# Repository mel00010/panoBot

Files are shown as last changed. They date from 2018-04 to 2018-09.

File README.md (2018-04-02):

# panoBot

## Summary of main responsiblities
- John (OLED display)
- Ben (PID loop)
- Zach (Servo movement/control)
- Justin (Button control)
- Mel (Hardware, main control flow)

## Update Monday March 12th
- Entire directory structure refactored to add some consistency
- Wrote Camera library to control the camera
- Started work on writing main()
- Wrote numerous utility functions as the avr-g++ compiler does not provide any of the C++ standard library headers
- Expanded and updated build system
- Modified build process to enable debugging, and create a target with debugging symbols included.  

## Update Sunday March 11th
- Servo controls for the most part figured out, still need to fine tune timings with hardwarde, but servos now have the ability to update/calculate their angles

- Buttons are finished may need to fine tune the debounce timings as needed, but outputting the correct information

- Screen code started, menu logic is still needed.

- Hardware debugger has arrived and finishing up final hardware configuration, planning on fine tuning with the hardware the upcomming week

- certain moving parts/cases are needing to be printed, planning on doing this Monday 03/12

## Update Sunday March 4th
- Update on project status: Due to hardware issues, the project has been reformed... we are now focusing on the firmware (Interfacing the Arduino board with the physical components: Buttons, toggle switch, servo, led display)

- The board as of Friday March 2 has been updated and is ready to undergo final testing. We now have a proper debugger for the board and can begin testing soft/hardware to ensure it will work properly.

- A PID(Proportion integral derivative) loop has been created to ensure servos will move to the appropriate place

- Button/Toggle switches are 90% done, all code is working (abstractly) but delay timings and port/switch numbers will be fine tuned later.

- Button debounce(noise reduction) implemented through software, this may need to be fine tuned, but will update as needed

- Servo timings have been selected, the prescaler , WGM (Wave Generation Mode) type has been selected 

- Physical display has minimal work, but as the deadline moves closer and members finish we will have multiple people working on the display

- Current goals: Finish rough draft of firmware, test with the board and fine tune timings. 

- Update although Google protobuf was originally planned as part of the project, as a way to interact with the panobot through a laptop, this has been put on hold while we ensure the firmware works properly. If adequate time is left over we will resume working on laptop/panobot interactions

## Update Sunday February 26th

- Spent most of the week working on hardware, the majority of which is complete
- Protobuff created for servo movement , camera communication
- GUI Template done, without buttons, this will be on hold until command line is more refined
(Zach , Ben , Justin, Mel)

## Update Sunday February 18th

- decided on google protobuf syntax/types
- Starting/Stopping 
- Movement:
	Elevation angle, servo angle
- Camera interactions:
	Focus
	Shutter
We all went through the tutorial for protobuf and made sure it is installed correctly/we are all using the correct documentation.

## The circuit board has been designed and built.

## Decided on using GTK+ for GUI, began work on GUI, currently in a rough mockup stage.
(Zach, Ben, Justin , Mel, John)

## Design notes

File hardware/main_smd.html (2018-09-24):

Partlist exported from /home/mel/eagle/projects/panoBot/main_smd.sch at 6/14/18 3:39 AM

Part | Value | Device | Package | Description | ALLIED_NUMBER | ALLIED_PRICE/STOCK | ARROW_PART_NUMBER | ARROW_PRICE/STOCK | AVAILABILITY | CENTERLINE_PITCH | COMMENT | DATASHEET | DESCRIPTION | DISTRIBUTOR1 | DISTRIBUTOR2 | GEOMETRY_HEIGHT | HEIGHT | MANUFACTURER | MANUFACTURER_NAME | MANUFACTURER_PART_NUMBER | MF | MP | MPN | NUMBER_OF_POSITIONS | ORDERCODE-DISTRI1 | ORDERCODE-DISTRI2 | ORDERCODE-MANU1 | PACKAGE | PARTNUMBER | PRICE | PRODUCT_TYPE | PROD_ID | RS_PART_NUMBER | RS_PRICE/STOCK | SF_ID | SPICEPREFIX | VALUE | VENDOR
+ | | 3,81/1,1 | 3,81/1,1 | THROUGH-HOLE PAD
- | | 3,81/1,1 | 3,81/1,1 | THROUGH-HOLE PAD
C1 | 0.1uF | 0.1UF-0603-100V-10% | 0603 | 0.1µF ceramic capacitors | | | | | | | | | | | | | | | | | | | | | | | | | | | | CAP-08390 | | | | | 0.1uF
C2 | 1.0uF | 1.0UF-0603-16V-10% | 0603 | 1µF ceramic capacitors | | | | | | | | | | | | | | | | | | | | | | | | | | | | CAP-00868 | | | | | 1.0uF
C3 | 10nF | 10NF-0603-50V-10% | 0603 | 0.01uF/10nF/10,000pF ceramic capacitors | | | | | | | | | | | | | | | | | | | | | | | | | | | | CAP-00867 | | | | | 10nF
C4 | 0.1uF | 0.1UF-0402-16V-10% | 0402 | 0.1µF ceramic capacitors | | | | | | | | | | | | | | | | | | | | | | | | | | | | CAP-12416 | | | | | 0.1uF
C5 | 0.1uF | 0.1UF-0402-16V-10% | 0402 | 0.1µF ceramic capacitors | | | | | | | | | | | | | | | | | | | | | | | | | | | | CAP-12416 | | | | | 0.1uF
C6 | 10uF | 10UF-0603-6.3V-20% | 0603 | 10.0µF ceramic capacitors | | | | | | | | | | | | | | | | | | | | | | | | | | | | CAP-11015 | | | | | 10uF
C7 | 0.1uF | 0.1UF-0402-16V-10% | 0402 | 0.1µF ceramic capacitors | | | | | | | | | | | | | | | | | | | | | | | | | | | | CAP-12416 | | | | | 0.1uF
C8 | 470nF | 470NF-0402-16V-10% | 0402 | 0.47uF/470nF ceramic capacitors | | | | | | | | | | | | | | | | | | | | | | | | | | | | CAP-09041 | | | | | 470nF
C9 | 0.1uF | 0.1UF-0402-16V-10% | 0402 | 0.1µF ceramic capacitors | | | | | | | | | | | | | | | | | | | | | | | | | | | | CAP-12416 | | | | | 0.1uF
C10 | 10nF | 10NF-0603-50V-10% | 0603 | 0.01uF/10nF/10,000pF ceramic capacitors | | | | | | | | | | | | | | | | | | | | | | | | | | | | CAP-00867 | | | | | 10nF
C11 | 10nF | 10NF-0603-50V-10% | 0603 | 0.01uF/10nF/10,000pF ceramic capacitors | | | | | | | | | | | | | | | | | | | | | | | | | | | | CAP-00867 | | | | | 10nF
C12 | 10nF | 10NF-0603-50V-10% | 0603 | 0.01uF/10nF/10,000pF ceramic capacitors | | | | | | | | | | | | | | | | | | | | | | | | | | | | CAP-00867 | | | | | 10nF
C13 | 10uF | 10UF-1210-50V-20% | 1210 | 10.0µF ceramic capacitors | | | | | | | | | | | | | | | | | | | | | | | | | | | | CAP-09824 | | | | | 10uF
C14 | 0.22uF | 0.22UF-0603-25V-10% | 0603 | 0.22µF ceramic capacitors | | | | | | | | | | | | | | | | | | | | | | | | | | | | CAP-07822 | | | | | 0.22uF
C15 | 0.1uF | 0.1UF-0402-16V-10% | 0402 | 0.1µF ceramic capacitors | | | | | | | | | | | | | | | | | | | | | | | | | | | | CAP-12416 | | | | | 0.1uF
C16 | 0.22uF | 0.22UF-0603-25V-10% | 0603 | 0.22µF ceramic capacitors | | | | | | | | | | | | | | | | | | | | | | | | | | | | CAP-07822 | | | | | 0.22uF
C17 | 0.1uF | 0.1UF-0402-16V-10% | 0402 | 0.1µF ceramic capacitors | | | | | | | | | | | | | | | | | | | | | | | | | | | | CAP-12416 | | | | | 0.1uF
C18 | 0.22uF | 0.22UF-0603-25V-10% | 0603 | 0.22µF ceramic capacitors | | | | | | | | | | | | | | | | | | | | | | | | | | | | CAP-07822 | | | | | 0.22uF
C19 | 1.0uF | 1.0UF-1206-50V-10% | 1206 | 1µF ceramic capacitors | | | | | | | | | | | | | | | | | | | | | | | | | | | | CAP-09822 | | | | | 1.0uF
C20 | 10nF | 10NF-0603-50V-10% | 0603 | 0.01uF/10nF/10,000pF ceramic capacitors | | | | | | | | | | | | | | | | | | | | | | | | | | | | CAP-00867 | | | | | 10nF
C21 | 0.1uF | C-EU075-052X106 | C075-052X106 | CAPACITOR, European symbol | | | | | | | | | | | | | | | | | | | | | | | | | | | | | | | | C
C22 | 1uF | CPOL-US085CS-1AR | 085CS_1AR | POLARIZED CAPACITOR, American symbol
C23 | 10uF | CPOL-US085CS-1AR | 085CS_1AR | POLARIZED CAPACITOR, American symbol
C24 | 10nF | 10NF-0603-50V-10% | 0603 | 0.01uF/10nF/10,000pF ceramic capacitors | | | | | | | | | | | | | | | | | | | | | | | | | | | | CAP-00867 | | | | | 10nF
C25 | 10nF | 10NF-0603-50V-10% | 0603 | 0.01uF/10nF/10,000pF ceramic capacitors | | | | | | | | | | | | | | | | | | | | | | | | | | | | CAP-00867 | | | | | 10nF
C26 | 0.1uF | 0.1UF-0402-16V-10% | 0402 | 0.1µF ceramic capacitors | | | | | | | | | | | | | | | | | | | | | | | | | | | | CAP-12416 | | | | | 0.1uF
C27 | 0.1uF | 0.1UF-0402-16V-10% | 0402 | 0.1µF ceramic capacitors | | | | | | | | | | | | | | | | | | | | | | | | | | | | CAP-12416 | | | | | 0.1uF
C28 | 0.1uF | 0.1UF-0402-16V-10% | 0402 | 0.1µF ceramic capacitors | | | | | | | | | | | | | | | | | | | | | | | | | | | | CAP-12416 | | | | | 0.1uF
C29 | 0.1uF | 0.1UF-0402-16V-10% | 0402 | 0.1µF ceramic capacitors | | | | | | | | | | | | | | | | | | | | | | | | | | | | CAP-12416 | | | | | 0.1uF
C30 | 4.7uF | 4.7UF0603 | 0603 | 4.7µF ceramic capacitors | | | | | | | | | | | | | | | | | | | | | | | | | | | | CAP-08280 | | | | | 4.7uF
C31 | 10nF | 10NF-0603-50V-10% | 0603 | 0.01uF/10nF/10,000pF ceramic capacitors | | | | | | | | | | | | | | | | | | | | | | | | | | | | CAP-00867 | | | | | 10nF
C32 | 10nF | 10NF-0603-50V-10% | 0603 | 0.01uF/10nF/10,000pF ceramic capacitors | | | | | | | | | | | | | | | | | | | | | | | | | | | | CAP-00867 | | | | | 10nF
C33 | 0.1uF | 0.1UF-0603-25V-(+80/-20%) | 0603 | 0.1µF ceramic capacitors | | | | | | | | | | | | | | | | | | | | | | | | | | | | CAP-00810 | | | | | 0.1uF
C34 | 0.1uF | 0.1UF-0603-25V-(+80/-20%) | 0603 | 0.1µF ceramic capacitors | | | | | | | | | | | | | | | | | | | | | | | | | | | | CAP-00810 | | | | | 0.1uF
C35 | 10nF | 10NF-0603-50V-10% | 0603 | 0.01uF/10nF/10,000pF ceramic capacitors | | | | | | | | | | | | | | | | | | | | | | | | | | | | CAP-00867 | | | | | 10nF
C36 | 10nF | 10NF-0603-50V-10% | 0603 | 0.01uF/10nF/10,000pF ceramic capacitors | | | | | | | | | | | | | | | | | | | | | | | | | | | | CAP-00867 | | | | | 10nF
C37 | 10nF | 10NF-0603-50V-10% | 0603 | 0.01uF/10nF/10,000pF ceramic capacitors | | | | | | | | | | | | | | | | | | | | | | | | | | | | CAP-00867 | | | | | 10nF
C38 | 10uF | 10UF-1210-50V-20% | 1210 | 10.0µF ceramic capacitors | | | | | | | | | | | | | | | | | | | | | | | | | | | | CAP-09824 | | | | | 10uF
C39 | 0.1uF | 0.1UF-0603-100V-10% | 0603 | 0.1µF ceramic capacitors | | | | | | | | | | | | | | | | | | | | | | | | | | | | CAP-08390 | | | | | 0.1uF
C40 | 10uF | 10UF-1210-50V-20% | 1210 | 10.0µF ceramic capacitors | | | | | | | | | | | | | | | | | | | | | | | | | | | | CAP-09824 | | | | | 10uF
C41 | 0.1uF | 0.1UF-0603-100V-10% | 0603 | 0.1µF ceramic capacitors | | | | | | | | | | | | | | | | | | | | | | | | | | | | CAP-08390 | | | | | 0.1uF
C42 | 10uF | 10UF-1210-50V-20% | 1210 | 10.0µF ceramic capacitors | | | | | | | | | | | | | | | | | | | | | | | | | | | | CAP-09824 | | | | | 10uF
C43 | 0.1uF | 0.1UF-0603-100V-10% | 0603 | 0.1µF ceramic capacitors | | | | | | | | | | | | | | | | | | | | | | | | | | | | CAP-08390 | | | | | 0.1uF
C44 | 22UF-1210-16V-20% | 22UF-1210-16V-20% | 1210 | 22µF ceramic capacitors
C45 | 22UF-1210-16V-20% | 22UF-1210-16V-20% | 1210 | 22µF ceramic capacitors
C46 | 22UF-1210-16V-20% | 22UF-1210-16V-20% | 1210 | 22µF ceramic capacitors
C47 | 22UF-1210-16V-20% | 22UF-1210-16V-20% | 1210 | 22µF ceramic capacitors
C48 | 22UF-1210-16V-20% | 22UF-1210-16V-20% | 1210 | 22µF ceramic capacitors
C49 | 22UF-1210-16V-20% | 22UF-1210-16V-20% | 1210 | 22µF ceramic capacitors
C50 | 0.1uF | 0.1UF-0402-16V-10% | 0402 | 0.1µF ceramic capacitors | | | | | | | | | | | | | | | | | | | | | | | | | | | | CAP-12416 | | | | | 0.1uF
C51 | 0.1uF | 0.1UF-0402-16V-10% | 0402 | 0.1µF ceramic capacitors | | | | | | | | | | | | | | | | | | | | | | | | | | | | CAP-12416 | | | | | 0.1uF
C52 | 0.1uF | 0.1UF-0402-16V-10% | 0402 | 0.1µF ceramic capacitors | | | | | | | | | | | | | | | | | | | | | | | | | | | | CAP-12416 | | | | | 0.1uF
C53 | 1800pF | C-EUC0402 | C0402 | CAPACITOR, European symbol
C54 | 91pF | C-EUC0402 | C0402 | CAPACITOR, European symbol
C55 | 2200pF | C-EUC0402 | C0402 | CAPACITOR, European symbol
C56 | 100pF | C-EUC0402 | C0402 | CAPACITOR, European symbol
C57 | 5600pF | C-EUC0402 | C0402 | CAPACITOR, European symbol
C58 | 330pF | C-EUC0402 | C0402 | CAPACITOR, European symbol
C59 | 0.1uF | 0.1UF-0603-25V-5% | 0603 | 0.1µF ceramic capacitors | | | | | | | | | | | | | | | | | | | | | | | | | | | | CAP-08604 | | | | | 0.1uF
C60 | 0.1uF | 0.1UF-0603-25V-5% | 0603 | 0.1µF ceramic capacitors | | | | | | | | | | | | | | | | | | | | | | | | | | | | CAP-08604 | | | | | 0.1uF
C61 | 0.1uF | 0.1UF-0603-25V-5% | 0603 | 0.1µF ceramic capacitors | | | | | | | | | | | | | | | | | | | | | | | | | | | | CAP-08604 | | | | | 0.1uF
C62 | 220pF | C-EUC0402 | C0402 | CAPACITOR, European symbol
C63 | 220pF | C-EUC0402 | C0402 | CAPACITOR, European symbol
C64 | 1.0uF | 1.0UF-1206-50V-10% | 1206 | 1µF ceramic capacitors | | | | | | | | | | | | | | | | | | | | | | | | | | | | CAP-09822 | | | | | 1.0uF
C65 | 10uF | 10UF-1210-50V-20% | 1210 | 10.0µF ceramic capacitors | | | | | | | | | | | | | | | | | | | | | | | | | | | | CAP-09824 | | | | | 10uF
C66 | 1.0uF | 1.0UF-1206-50V-10% | 1206 | 1µF ceramic capacitors | | | | | | | | | | | | | | | | | | | | | | | | | | | | CAP-09822 | | | | | 1.0uF
C67 | 1.0uF | 1.0UF-1206-50V-10% | 1206 | 1µF ceramic capacitors | | | | | | | | | | | | | | | | | | | | | | | | | | | | CAP-09822 | | | | | 1.0uF
C68 | 1.0uF | 1.0UF-1206-50V-10% | 1206 | 1µF ceramic capacitors | | | | | | | | | | | | | | | | | | | | | | | | | | | | CAP-09822 | | | | | 1.0uF
C69 | 22UF-1210-16V-20% | 22UF-1210-16V-20% | 1210 | 22µF ceramic capacitors
C70 | 10uF | 10UF-1210-50V-20% | 1210 | 10.0µF ceramic capacitors | | | | | | | | | | | | | | | | | | | | | | | | | | | | CAP-09824 | | | | | 10uF
C71 | 0.1uF | 0.1UF-0603-25V-5% | 0603 | 0.1µF ceramic capacitors | | | | | | | | | | | | | | | | | | | | | | | | | | | | CAP-08604 | | | | | 0.1uF
C72 | 0.1uF | 0.1UF-0603-25V-5% | 0603 | 0.1µF ceramic capacitors | | | | | | | | | | | | | | | | | | | | | | | | | | | | CAP-08604 | | | | | 0.1uF
C73 | 0.22uF | 0.22UF-0603-25V-10% | 0603 | 0.22µF ceramic capacitors | | | | | | | | | | | | | | | | | | | | | | | | | | | | CAP-07822 | | | | | 0.22uF
C74 | 1.0uF | 1.0UF-0402-16V-10% | 0402 | 1µF ceramic capacitors | | | | | | | | | | | | | | | | | | | | | | | | | | | | CAP-12417 | | | | | 1.0uF
C75 | 10nF | 10NF-0603-50V-10% | 0603 | 0.01uF/10nF/10,000pF ceramic capacitors | | | | | | | | | | | | | | | | | | | | | | | | | | | | CAP-00867 | | | | | 10nF
D1 | MBRS340T3 | MBRS340T3 | SMC | SCHOTTKY BARRIER RECTIFIER 3.0 AMPERES 20, 30, 40 VOLT
D2 | 1N4002 | 1N4004 | DO41-10 | DIODE
D3 | 1N4002 | 1N4004 | DO41-10 | DIODE
FB1 | 30Ω/1.8A | FERRITE_BEAD-0603 | 0603 | Ferrite Bead (blocks, cores, rings, chokes, etc.) | | | | | | | | | | | | | | | | | | | | | | | | | | | | NDUC-07859 | | | | | 30Ω/1.8A
FOCUS | 4N35S | 4N35S | SOT23-6
IC0 | STM32F313VCT6 | STM32F313VCT6 | QFP50P1600X1600X160-100N
IC1 | S1315F8_RAW | S1315F8_RAW | S1315F8_SMT
IC2 | TMC262-LA | TMC262-LA | TMC_QFN32_0.5_5.0X5.0 | Energy saving high resolution microstepping two phase stepper driver with Step/Dir, SPI, up to 60V, QFN32(5x5) | | | | | | | | http://www_trinamic_com/_scripts/download_php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 | Energy saving high resolution microstepping two phase stepper driver with Step/Dir, SPI, up to 60V, QFN32(5x5) | Digikey | Farnell | 0,9mm | | TRINAMIC | | | | | | | 1460-1044-ND | 1858307 | TMC262-LA | | | | | | | | | | TMC262-LA
IC3 | TMC262-LA | TMC262-LA | TMC_QFN32_0.5_5.0X5.0 | Energy saving high resolution microstepping two phase stepper driver with Step/Dir, SPI, up to 60V, QFN32(5x5) | | | | | | | | http://www_trinamic_com/_scripts/download_php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 | Energy saving high resolution microstepping two phase stepper driver with Step/Dir, SPI, up to 60V, QFN32(5x5) | Digikey | Farnell | 0,9mm | | TRINAMIC | | | | | | | 1460-1044-ND | 1858307 | TMC262-LA | | | | | | | | | | TMC262-LA
IC4 | TMC262-LA | TMC262-LA | TMC_QFN32_0.5_5.0X5.0 | Energy saving high resolution microstepping two phase stepper driver with Step/Dir, SPI, up to 60V, QFN32(5x5) | | | | | | | | http://www_trinamic_com/_scripts/download_php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 | Energy saving high resolution microstepping two phase stepper driver with Step/Dir, SPI, up to 60V, QFN32(5x5) | Digikey | Farnell | 0,9mm | | TRINAMIC | | | | | | | 1460-1044-ND | 1858307 | TMC262-LA | | | | | | | | | | TMC262-LA
IC5 | TMC424 | TMC424 | TMC_TQFP100_0.5_14X14 | Serial triple Incremental Encoder Interface; TQ100 | | | | | | | | http://www_trinamic_com/_scripts/download_php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 | Serial triple Incremental Encoder Interface | TQ100 | Digikey | Farnell | 1_6mm | | TRINAMIC | | | | | | | 1460-1046-ND | | TMC424 | | | | | | | | | | TMC424
IC6 | TMC429-PI24 | TMC429-PI24 | TMC_SO24_SOT137-1_1.27_15.5X7.5 | Intelligent Triple Stepper Motor Controller with SPI, Step/Dir, SOP24 | | | | | | | | http://www_trinamic_com/_scripts/download_php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 | Intelligent Triple Stepper Motor Controller with SPI, Step/Dir, SOP24 | Digikey | Farnell | 2,65mm | | TRINAMIC | | | | | | | 1460-1058-5-ND | 1858309 | TMC429-PI24 | | | | | | | | | | TMC429-PI24
IC8 | LM317MBSTT3 | LM317MBSTT3 | SOT223 | 500 mA Adjustable Output Positive Voltage Regulator | | | | | | | | | | | | | | | | | | | | | | | | | LM317M
J1 | POWER_JACKPTH_BREAD | POWER_JACKPTH_BREAD | POWER_JACK_PTH_BREAD | Power Jack Connector | | | | | | | | | | | | | | | | | | | | | | | | | | | | PRT-10811
J2 | | CONN_05X2SHD_LOCK | 2X5-SHROUDED_LOCK | Multi connection point. Often used as Generic Header-pin footprint for 0.1 inch spaced/style header connections | | | | | | | | | | | | | | | | | | | | | | | | | | | | CONN-08671 | | | PRT-08506
J3 | Motor Coil B | SCREW-TERMINAL-GREEN(2P-5.0) | H2-5.0-10.5X8.0MM | 320110031 | | | | | | | | | | | | | | | | | | | | | | | | | | | | | | | | | GREEN-2P-5.0
J4 | Motor Coil A | SCREW-TERMINAL-GREEN(2P-5.0) | H2-5.0-10.5X8.0MM | 320110031 | | | | | | | | | | | | | | | | | | | | | | | | | | | | | | | | | GREEN-2P-5.0
J5 | 73100-0114 | 73100-0114 | 73100-0114 | Molex Right Angle 50ohm | 70357943 | http://www.alliedelec.com/molex-incorporated-73100-0114/70357943/ | 73100-0114 | http://uk.rs-online.com/web/p/products/7595252P | | | | | Molex Right Angle 50ohm | | | | mm | | Molex | 73100-0114 | | | | | | | | | | | | | 7595252P | http://uk.rs-online.com/web/p/products/7595252P
J8 | | CONN_05 | 1X05 | Multi connection point. Often used as Generic Header-pin footprint for 0.1 inch spaced/style header connections
J9 | Motor Coil B | SCREW-TERMINAL-GREEN(2P-5.0) | H2-5.0-10.5X8.0MM | 320110031 | | | | | | | | | | | | | | | | | | | | | | | | | | | | | | | | | GREEN-2P-5.0
J10 | Motor Coil A | SCREW-TERMINAL-GREEN(2P-5.0) | H2-5.0-10.5X8.0MM | 320110031 | | | | | | | | | | | | | | | | | | | | | | | | | | | | | | | | | GREEN-2P-5.0
J11 | Motor Coil B | SCREW-TERMINAL-GREEN(2P-5.0) | H2-5.0-10.5X8.0MM | 320110031 | | | | | | | | | | | | | | | | | | | | | | | | | | | | | | | | | GREEN-2P-5.0
J12 | Motor Coil A | SCREW-TERMINAL-GREEN(2P-5.0) | H2-5.0-10.5X8.0MM | 320110031 | | | | | | | | | | | | | | | | | | | | | | | | | | | | | | | | | GREEN-2P-5.0
J13 | | CONN_05 | 1X05 | Multi connection point. Often used as Generic Header-pin footprint for 0.1 inch spaced/style header connections
J14 | | CONN_05 | 1X05 | Multi connection point. Often used as Generic Header-pin footprint for 0.1 inch spaced/style header connections
JP1 | | JP1Q | JP1 | JUMPER
L3 | 10UH-225MA | SMD-INDUCTOR-10UH-225MA-10%(0806) | L0806 | 303010042 | | | | | | | | | | | | | | | | | | | LQH2MCN100K02L | | | | | | | | | | | | | | 10UH-225MA
L4 | 10UH-225MA | SMD-INDUCTOR-10UH-225MA-10%(0806) | L0806 | 303010042 | | | | | | | | | | | | | | | | | | | LQH2MCN100K02L | | | | | | | | | | | | | | 10UH-225MA
L5 | 10UH-225MA | SMD-INDUCTOR-10UH-225MA-10%(0806) | L0806 | 303010042 | | | | | | | | | | | | | | | | | | | LQH2MCN100K02L | | | | | | | | | | | | | | 10UH-225MA
P1 | 1-2295018-2 | 1-2295018-2 | TE_1-2295018-2 | Conn USB Type C RCP 12 POS Solder RA SMD 12 Terminal 1 Port T/R | | | | | Good | .5 mm[.019 in] | 1-2295018-2 | | USB TYPE C, REC OFFSET 0.65MM DUAL SMT | | | | | | | | TE Connectivity | 1-2295018-2 | | 24 | | | | None | | 1.70 USD | Connector
Q1 | AOD4189 | AOD4189 | TO252
Q2 | AOD4189 | AOD4189 | TO252
Q3 | AOD4184A | AOD4184A | TO252
Q4 | AOD4184A | AOD4184A | TO252
Q5 | AOD4184A | AOD4184A | TO252
Q6 | AOD4184A | AOD4184A | TO252
Q7 | AOD4189 | AOD4189 | TO252
Q8 | AOD4189 | AOD4189 | TO252
Q9 | AOD4189 | AOD4189 | TO252
Q10 | AOD4189 | AOD4189 | TO252
Q11 | AOD4184A | AOD4184A | TO252
Q12 | AOD4184A | AOD4184A | TO252
Q13 | AOD4184A | AOD4184A | TO252
Q14 | AOD4184A | AOD4184A | TO252
Q15 | AOD4189 | AOD4189 | TO252
Q16 | AOD4189 | AOD4189 | TO252
Q17 | AOD4189 | AOD4189 | TO252
Q18 | AOD4189 | AOD4189 | TO252
Q19 | AOD4184A | AOD4184A | TO252
Q20 | AOD4184A | AOD4184A | TO252
Q21 | AOD4184A | AOD4184A | TO252
Q22 | AOD4184A | AOD4184A | TO252
Q23 | AOD4189 | AOD4189 | TO252
Q24 | AOD4189 | AOD4189 | TO252
R1 | 100K | 100KOHM-0402-1/16W-1% | 0402 | 100kΩ resistor | | | | | | | | | | | | | | | | | | | | | | | | | | | | RES-13495 | | | | | 100K
R6 | 10k | 10KOHM-0603-1/10W-1% | 0603 | 10kΩ resistor | | | | | | | | | | | | | | | | | | | | | | | | | | | | RES-00824 | | | | | 10k
R7 | 0.1 | 0.1OHM-1210-1/2W-1% | 1210 | 0.1Ω resistor | | | | | | | | | | | | | | | | | | | | | | | | | | | | RES-12374 | | | | | 0.1
R8 | 0.1 | 0.1OHM-1210-1/2W-1% | 1210 | 0.1Ω resistor | | | | | | | | | | | | | | | | | | | | | | | | | | | | RES-12374 | | | | | 0.1
R9 | 220 | 220OHM-0603-1/10W-1% | 0603 | 220Ω resistor | | | | | | | | | | | | | | | | | | | | | | | | | | | | RES-07861 | | | | | 220
R10 | 220 | 220OHM-0603-1/10W-1% | 0603 | 220Ω resistor | | | | | | | | | | | | | | | | | | | | | | | | | | | | RES-07861 | | | | | 220
R11 | 10k | 10KOHM-0603-1/10W-1% | 0603 | 10kΩ resistor | | | | | | | | | | | | | | | | | | | | | | | | | | | | RES-00824 | | | | | 10k
R12 | 10k | 10KOHM-0603-1/10W-1% | 0603 | 10kΩ resistor | | | | | | | | | | | | | | | | | | | | | | | | | | | | RES-00824 | | | | | 10k
R13 | 10k | 10KOHM-0603-1/10W-1% | 0603 | 10kΩ resistor | | | | | | | | | | | | | | | | | | | | | | | | | | | | RES-00824 | | | | | 10k
R14 | 10k | 10KOHM-0603-1/10W-1% | 0603 | 10kΩ resistor | | | | | | | | | | | | | | | | | | | | | | | | | | | | RES-00824 | | | | | 10k
R15 | 10 | 10OHM-1206-1/4W-1% | 1206 | 10Ω resistor | | | | | | | | | | | | | | | | | | | | | | | | | | | | RES-08705 | | | | | 10
R16 | 10 | 10OHM-1206-1/4W-1% | 1206 | 10Ω resistor | | | | | | | | | | | | | | | | | | | | | | | | | | | | RES-08705 | | | | | 10
R17 | 10k | 10KOHM-0603-1/10W-1% | 0603 | 10kΩ resistor | | | | | | | | | | | | | | | | | | | | | | | | | | | | RES-00824 | | | | | 10k
R18 | 10k | 10KOHM-0603-1/10W-1% | 0603 | 10kΩ resistor | | | | | | | | | | | | | | | | | | | | | | | | | | | | RES-00824 | | | | | 10k
R19 | 0.1 | 0.1OHM-1210-1/2W-1% | 1210 | 0.1Ω resistor | | | | | | | | | | | | | | | | | | | | | | | | | | | | RES-12374 | | | | | 0.1
R20 | 0.1 | 0.1OHM-1210-1/2W-1% | 1210 | 0.1Ω resistor | | | | | | | | | | | | | | | | | | | | | | | | | | | | RES-12374 | | | | | 0.1
R21 | 1M | 1MOHM-0603-1/4W-5% | 0603 | 1MΩ resistor | | | | | | | | | | | | | | | | | | | | | | | | | | | | RES-07868 | | | | | 1M
R22 | 10k | 10KOHM-0603-1/10W-1% | 0603 | 10kΩ resistor | | | | | | | | | | | | | | | | | | | | | | | | | | | | RES-00824 | | | | | 10k
R23 | 0.1 | 0.1OHM-1210-1/2W-1% | 1210 | 0.1Ω resistor | | | | | | | | | | | | | | | | | | | | | | | | | | | | RES-12374 | | | | | 0.1
R24 | 0.1 | 0.1OHM-1210-1/2W-1% | 1210 | 0.1Ω resistor | | | | | | | | | | | | | | | | | | | | | | | | | | | | RES-12374 | | | | | 0.1
R25 | 10 | 10OHM-1206-1/4W-1% | 1206 | 10Ω resistor | | | | | | | | | | | | | | | | | | | | | | | | | | | | RES-08705 | | | | | 10
R26 | 10 | 10OHM-1206-1/4W-1% | 1206 | 10Ω resistor | | | | | | | | | | | | | | | | | | | | | | | | | | | | RES-08705 | | | | | 10
R27 | 100k | 100KOHM-0603-1/10W-1% | 0603 | 100kΩ resistor | | | | | | | | | | | | | | | | | | | | | | | | | | | | RES-07828 | | | | | 100k
R28 | 0.01R | RESISTOR0805 | 0805 | Generic Resistor Package
R29 | 240Ω | R-US_M0805 | M0805 | RESISTOR, American symbol
R30 | 48Ω | R-US_M0805 | M0805 | RESISTOR, American symbol
R31 | 10k | 10KOHM-0603-1/10W-1% | 0603 | 10kΩ resistor | | | | | | | | | | | | | | | | | | | | | | | | | | | | RES-00824 | | | | | 10k
R32 | 10k | 10KOHM-0603-1/10W-1% | 0603 | 10kΩ resistor | | | | | | | | | | | | | | | | | | | | | | | | | | | | RES-00824 | | | | | 10k
R33 | 10 | 10OHM-1206-1/4W-1% | 1206 | 10Ω resistor | | | | | | | | | | | | | | | | | | | | | | | | | | | | RES-08705 | | | | | 10
R34 | 10 | 10OHM-1206-1/4W-1% | 1206 | 10Ω resistor | | | | | | | | | | | | | | | | | | | | | | | | | | | | RES-08705 | | | | | 10
R37 | 1M | 1MOHM-0603-1/4W-5% | 0603 | 1MΩ resistor | | | | | | | | | | | | | | | | | | | | | | | | | | | | RES-07868 | | | | | 1M
R38 | 1M | 1MOHM-0603-1/4W-5% | 0603 | 1MΩ resistor | | | | | | | | | | | | | | | | | | | | | | | | | | | | RES-07868 | | | | | 1M
R39 | 47k | 47KOHM-0603-1/10W-1% | 0603 | 47kΩ resistor | | | | | | | | | | | | | | | | | | | | | | | | | | | | RES-07871 | | | | | 47k
R40 | 47k | 47KOHM-0603-1/10W-1% | 0603 | 47kΩ resistor | | | | | | | | | | | | | | | | | | | | | | | | | | | | RES-07871 | | | | | 47k
R41 | 47k | 47KOHM-0603-1/10W-1% | 0603 | 47kΩ resistor | | | | | | | | | | | | | | | | | | | | | | | | | | | | RES-07871 | | | | | 47k
R42 | 9.53k | RESISTOR0603 | 0603 | Generic Resistor Package
R43 | 8.45k | RESISTOR0603 | 0603 | Generic Resistor Package
R44 | 2.74k | RESISTOR0603 | 0603 | Generic Resistor Package
R45 | 19.1k | RESISTOR0603 | 0603 | Generic Resistor Package
R46 | 100k | RESISTOR0603 | 0603 | Generic Resistor Package
R47 | 32.4k | RESISTOR0603 | 0603 | Generic Resistor Package
R48 | 100k | RESISTOR0603 | 0603 | Generic Resistor Package
R49 | 100k | RESISTOR0603 | 0603 | Generic Resistor Package
R50 | 7.15k | RESISTOR0603 | 0603 | Generic Resistor Package
R51 | 15k | 15KOHM-0603-1/10W-1% | 0603 | 15kΩ resistor | | | | | | | | | | | | | | | | | | | | | | | | | | | | RES-07854 | | | | | 15k
S1 | EN11-HSM1BF20 | EN11-HSM1BF20 | EN11HSM1BF20 | ENCODER 11MM ROTARY SW TOP ADJ | | | EN11-HSM1BF20 | | | | | | ENCODER 11MM ROTARY SW TOP ADJ | | | | 26mm | | TT Electronics/BI Magnetics | EN11-HSM1BF20
S2 | TL3342F160QG | TL3342F160QG | SW_TL3342F160QG | TL3342 Series SPST 1.6 N Round Button Gull Wing Surface Mount Tactile Switch | | | | | | | | | | | | | | E SWITCH
SCREEN1 | OLED | OLED | SIP-20
SHUTTER | 4N35S | 4N35S | SOT23-6
U$27 | CSD17309Q3 | CSD17309Q3 | DQG0008A | | | | | | | | | | | | | | | | | CSD17309Q3 | | | | | | | | | | | | | | | | | | Texas Instruments
U$28 | CSD17309Q3 | CSD17309Q3 | DQG0008A | | | | | | | | | | | | | | | | | CSD17309Q3 | | | | | | | | | | | | | | | | | | Texas Instruments
U$29 | TPS659821 | TPS659821 | QFN50P800X800X100-57N
U1 | TPD8S300RUKRRUK0020B_NV | TPD8S300RUKRRUK0020B_NV | RUK0020B_NV
U2 | FT232RL-REEL | FT232RL-REEL | SOP65P780X200-28N | USB Full Speed to Serial UART IC, Includes Oscillator and EEPROM - SSOP-28 | | | | | | | | | | | | | | Future Technology Devices International Ltd
U3 | CDCS502PWR | CDCS502PWR | SOP65P640X120-8N | Crystal Oscillator | | | | | Good | | | | Crystal Oscillator / Clock Generator with optional SSC 8-TSSOP -40 to 85 | | | | | | | | Texas Instruments | CDCS502PWR | | | | | | TSSOP-8 Texas Instruments | | 1.60 USD
U4 | LSM9DS1 | LSM9DS1 | PQFN24P43_350X300X102L35X23N | iNEMO inertial module: 3D accelerometer, 3D gyroscope, 3D magnetometer | | | | | Unavailable | | | | iNEMO inertial module: 3D accelerometer, 3D gyroscope, 3D magnetometer | | | | | | | | STMicroelectronics | LSM9DS1 | | | | | | None | | None
U5 | TPS54336ADRCR | TPS54336ADRCR | DRC0010J
U6 | TPS54336ADRCR | TPS54336ADRCR | DRC0010J
U7 | TPS54336ADRCR | TPS54336ADRCR | DRC0010J
X1 | STEREOJACK | STEREOJACK | STX3100 | MIC/HEADPHONE JACK
Y1 | 7B-16.000MAAJ-T | 7B-16.000MAAJ-T | 7B-16.000MAAJ-T_OSCSC500X320X105-4N | Crystal 16.0000mhz 18pf Smd | | | | | | | | | | | | | | TXC Corporation

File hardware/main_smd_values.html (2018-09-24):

Partlist exported from /home/mel/eagle/projects/panoBot/main_smd.sch at 6/14/18 3:39 AM

Qty | Value | Device | Package | Parts | Description | ALLIED_NUMBER | ALLIED_PRICE/STOCK | ARROW_PART_NUMBER | ARROW_PRICE/STOCK | AVAILABILITY | CENTERLINE_PITCH | COMMENT | DATASHEET | DESCRIPTION | DISTRIBUTOR1 | DISTRIBUTOR2 | GEOMETRY_HEIGHT | HEIGHT | MANUFACTURER | MANUFACTURER_NAME | MANUFACTURER_PART_NUMBER | MF | MP | MPN | NUMBER_OF_POSITIONS | ORDERCODE-DISTRI1 | ORDERCODE-DISTRI2 | ORDERCODE-MANU1 | PACKAGE | PARTNUMBER | PRICE | PRODUCT_TYPE | PROD_ID | RS_PART_NUMBER | RS_PRICE/STOCK | SF_ID | SPICEPREFIX | VALUE | VENDOR
2 | | 3,81/1,1 | 3,81/1,1 | +, - | THROUGH-HOLE PAD
3 | | CONN_05 | 1X05 | J8, J13, J14 | Multi connection point. Often used as Generic Header-pin footprint for 0.1 inch spaced/style header connections
1 | | CONN_05X2SHD_LOCK | 2X5-SHROUDED_LOCK | J2 | Multi connection point. Often used as Generic Header-pin footprint for 0.1 inch spaced/style header connections | | | | | | | | | | | | | | | | | | | | | | | | | | | | CONN-08671 | | | PRT-08506
1 | | JP1Q | JP1 | JP1 | JUMPER
3 | TMC262-LA | TMC262-LA | TMC_QFN32_0.5_5.0X5.0 | IC2, IC3, IC4 | Energy saving high resolution microstepping two phase stepper driver with Step/Dir, SPI, up to 60V, QFN32(5x5) | | | | | | | | http://www_trinamic_com/_scripts/download_php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 | Energy saving high resolution microstepping two phase stepper driver with Step/Dir, SPI, up to 60V, QFN32(5x5) | Digikey | Farnell | 0,9mm | | TRINAMIC | | | | | | | 1460-1044-ND | 1858307 | TMC262-LA | | | | | | | | | | TMC262-LA
1 | TMC424 | TMC424 | TMC_TQFP100_0.5_14X14 | IC5 | Serial triple Incremental Encoder Interface; TQ100 | | | | | | | | http://www_trinamic_com/_scripts/download_php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 | Serial triple Incremental Encoder Interface | TQ100 | Digikey | Farnell | 1_6mm | | TRINAMIC | | | | | | | 1460-1046-ND | | TMC424 | | | | | | | | | | TMC424
1 | TMC429-PI24 | TMC429-PI24 | TMC_SO24_SOT137-1_1.27_15.5X7.5 | IC6 | Intelligent Triple Stepper Motor Controller with SPI, Step/Dir, SOP24 | | | | | | | | http://www_trinamic_com/_scripts/download_php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 | Intelligent Triple Stepper Motor Controller with SPI, Step/Dir, SOP24 | Digikey | Farnell | 2,65mm | | TRINAMIC | | | | | | | 1460-1058-5-ND | 1858309 | TMC429-PI24 | | | | | | | | | | TMC429-PI24
1 | 0.01R | RESISTOR0805 | 0805 | R28 | Generic Resistor Package
6 | 0.1 | 0.1OHM-1210-1/2W-1% | 1210 | R7, R8, R19, R20, R23, R24 | 0.1Ω resistor | | | | | | | | | | | | | | | | | | | | | | | | | | | | RES-12374 | | | | | 0.1
13 | 0.1uF | 0.1UF-0402-16V-10% | 0402 | C4, C5, C7, C9, C15, C17, C26, C27, C28, C29, C50, C51, C52 | 0.1µF ceramic capacitors | | | | | | | | | | | | | | | | | | | | | | | | | | | | CAP-12416 | | | | | 0.1uF
4 | 0.1uF | 0.1UF-0603-100V-10% | 0603 | C1, C39, C41, C43 | 0.1µF ceramic capacitors | | | | | | | | | | | | | | | | | | | | | | | | | | | | CAP-08390 | | | | | 0.1uF
2 | 0.1uF | 0.1UF-0603-25V-(+80/-20%) | 0603 | C33, C34 | 0.1µF ceramic capacitors | | | | | | | | | | | | | | | | | | | | | | | | | | | | CAP-00810 | | | | | 0.1uF
5 | 0.1uF | 0.1UF-0603-25V-5% | 0603 | C59, C60, C61, C71, C72 | 0.1µF ceramic capacitors | | | | | | | | | | | | | | | | | | | | | | | | | | | | CAP-08604 | | | | | 0.1uF
1 | 0.1uF | C-EU075-052X106 | C075-052X106 | C21 | CAPACITOR, European symbol | | | | | | | | | | | | | | | | | | | | | | | | | | | | | | | | C
4 | 0.22uF | 0.22UF-0603-25V-10% | 0603 | C14, C16, C18, C73 | 0.22µF ceramic capacitors | | | | | | | | | | | | | | | | | | | | | | | | | | | | CAP-07822 | | | | | 0.22uF
1 | 1-2295018-2 | 1-2295018-2 | TE_1-2295018-2 | P1 | Conn USB Type C RCP 12 POS Solder RA SMD 12 Terminal 1 Port T/R | | | | | Good | .5 mm[.019 in] | 1-2295018-2 | | USB TYPE C, REC OFFSET 0.65MM DUAL SMT | | | | | | | | TE Connectivity | 1-2295018-2 | | 24 | | | | None | | 1.70 USD | Connector
1 | 1.0uF | 1.0UF-0402-16V-10% | 0402 | C74 | 1µF ceramic capacitors | | | | | | | | | | | | | | | | | | | | | | | | | | | | CAP-12417 | | | | | 1.0uF
1 | 1.0uF | 1.0UF-0603-16V-10% | 0603 | C2 | 1µF ceramic capacitors | | | | | | | | | | | | | | | | | | | | | | | | | | | | CAP-00868 | | | | | 1.0uF
5 | 1.0uF | 1.0UF-1206-50V-10% | 1206 | C19, C64, C66, C67, C68 | 1µF ceramic capacitors | | | | | | | | | | | | | | | | | | | | | | | | | | | | CAP-09822 | | | | | 1.0uF
6 | 10 | 10OHM-1206-1/4W-1% | 1206 | R15, R16, R25, R26, R33, R34 | 10Ω resistor | | | | | | | | | | | | | | | | | | | | | | | | | | | | RES-08705 | | | | | 10
1 | 100K | 100KOHM-0402-1/16W-1% | 0402 | R1 | 100kΩ resistor | | | | | | | | | | | | | | | | | | | | | | | | | | | | RES-13495 | | | | | 100K
1 | 100k | 100KOHM-0603-1/10W-1% | 0603 | R27 | 100kΩ resistor | | | | | | | | | | | | | | | | | | | | | | | | | | | | RES-07828 | | | | | 100k
3 | 100k | RESISTOR0603 | 0603 | R46, R48, R49 | Generic Resistor Package
1 | 100pF | C-EUC0402 | C0402 | C56 | CAPACITOR, European symbol
3 | 10UH-225MA | SMD-INDUCTOR-10UH-225MA-10%(0806) | L0806 | L3, L4, L5 | 303010042 | | | | | | | | | | | | | | | | | | | LQH2MCN100K02L | | | | | | | | | | | | | | 10UH-225MA
10 | 10k | 10KOHM-0603-1/10W-1% | 0603 | R6, R11, R12, R13, R14, R17, R18, R22, R31, R32 | 10kΩ resistor | | | | | | | | | | | | | | | | | | | | | | | | | | | | RES-00824 | | | | | 10k
13 | 10nF | 10NF-0603-50V-10% | 0603 | C3, C10, C11, C12, C20, C24, C25, C31, C32, C35, C36, C37, C75 | 0.01uF/10nF/10,000pF ceramic capacitors | | | | | | | | | | | | | | | | | | | | | | | | | | | | CAP-00867 | | | | | 10nF
1 | 10uF | 10UF-0603-6.3V-20% | 0603 | C6 | 10.0µF ceramic capacitors | | | | | | | | | | | | | | | | | | | | | | | | | | | | CAP-11015 | | | | | 10uF
6 | 10uF | 10UF-1210-50V-20% | 1210 | C13, C38, C40, C42, C65, C70 | 10.0µF ceramic capacitors | | | | | | | | | | | | | | | | | | | | | | | | | | | | CAP-09824 | | | | | 10uF
1 | 10uF | CPOL-US085CS-1AR | 085CS_1AR | C23 | POLARIZED CAPACITOR, American symbol
1 | 15k | 15KOHM-0603-1/10W-1% | 0603 | R51 | 15kΩ resistor | | | | | | | | | | | | | | | | | | | | | | | | | | | | RES-07854 | | | | | 15k
1 | 1800pF | C-EUC0402 | C0402 | C53 | CAPACITOR, European symbol
1 | 19.1k | RESISTOR0603 | 0603 | R45 | Generic Resistor Package
3 | 1M | 1MOHM-0603-1/4W-5% | 0603 | R21, R37, R38 | 1MΩ resistor | | | | | | | | | | | | | | | | | | | | | | | | | | | | RES-07868 | | | | | 1M
2 | 1N4002 | 1N4004 | DO41-10 | D2, D3 | DIODE
1 | 1uF | CPOL-US085CS-1AR | 085CS_1AR | C22 | POLARIZED CAPACITOR, American symbol
1 | 2.74k | RESISTOR0603 | 0603 | R44 | Generic Resistor Package
2 | 220 | 220OHM-0603-1/10W-1% | 0603 | R9, R10 | 220Ω resistor | | | | | | | | | | | | | | | | | | | | | | | | | | | | RES-07861 | | | | | 220
1 | 2200pF | C-EUC0402 | C0402 | C55 | CAPACITOR, European symbol
2 | 220pF | C-EUC0402 | C0402 | C62, C63 | CAPACITOR, European symbol
7 | 22UF-1210-16V-20% | 22UF-1210-16V-20% | 1210 | C44, C45, C46, C47, C48, C49, C69 | 22µF ceramic capacitors
1 | 240Ω | R-US_M0805 | M0805 | R29 | RESISTOR, American symbol
1 | 30Ω/1.8A | FERRITE_BEAD-0603 | 0603 | FB1 | Ferrite Bead (blocks, cores, rings, chokes, etc.) | | | | | | | | | | | | | | | | | | | | | | | | | | | | NDUC-07859 | | | | | 30Ω/1.8A
1 | 32.4k | RESISTOR0603 | 0603 | R47 | Generic Resistor Package
1 | 330pF | C-EUC0402 | C0402 | C58 | CAPACITOR, European symbol
1 | 4.7uF | 4.7UF0603 | 0603 | C30 | 4.7µF ceramic capacitors | | | | | | | | | | | | | | | | | | | | | | | | | | | | CAP-08280 | | | | | 4.7uF
1 | 470nF | 470NF-0402-16V-10% | 0402 | C8 | 0.47uF/470nF ceramic capacitors | | | | | | | | | | | | | | | | | | | | | | | | | | | | CAP-09041 | | | | | 470nF
3 | 47k | 47KOHM-0603-1/10W-1% | 0603 | R39, R40, R41 | 47kΩ resistor | | | | | | | | | | | | | | | | | | | | | | | | | | | | RES-07871 | | | | | 47k
1 | 48Ω | R-US_M0805 | M0805 | R30 | RESISTOR, American symbol
2 | 4N35S | 4N35S | SOT23-6 | FOCUS, SHUTTER
1 | 5600pF | C-EUC0402 | C0402 | C57 | CAPACITOR, European symbol
1 | 7.15k | RESISTOR0603 | 0603 | R50 | Generic Resistor Package
1 | 73100-0114 | 73100-0114 | 73100-0114 | J5 | Molex Right Angle 50ohm | 70357943 | http://www.alliedelec.com/molex-incorporated-73100-0114/70357943/ | 73100-0114 | http://uk.rs-online.com/web/p/products/7595252P | | | | | Molex Right Angle 50ohm | | | | mm | | Molex | 73100-0114 | | | | | | | | | | | | | 7595252P | http://uk.rs-online.com/web/p/products/7595252P
1 | 7B-16.000MAAJ-T | 7B-16.000MAAJ-T | 7B-16.000MAAJ-T_OSCSC500X320X105-4N | Y1 | Crystal 16.0000mhz 18pf Smd | | | | | | | | | | | | | | TXC Corporation
1 | 8.45k | RESISTOR0603 | 0603 | R43 | Generic Resistor Package
1 | 9.53k | RESISTOR0603 | 0603 | R42 | Generic Resistor Package
1 | 91pF | C-EUC0402 | C0402 | C54 | CAPACITOR, European symbol
12 | AOD4184A | AOD4184A | TO252 | Q3, Q4, Q5, Q6, Q11, Q12, Q13, Q14, Q19, Q20, Q21, Q22
12 | AOD4189 | AOD4189 | TO252 | Q1, Q2, Q7, Q8, Q9, Q10, Q15, Q16, Q17, Q18, Q23, Q24
1 | CDCS502PWR | CDCS502PWR | SOP65P640X120-8N | U3 | Crystal Oscillator | | | | | Good | | | | Crystal Oscillator / Clock Generator with optional SSC 8-TSSOP -40 to 85 | | | | | | | | Texas Instruments | CDCS502PWR | | | | | | TSSOP-8 Texas Instruments | | 1.60 USD
2 | CSD17309Q3 | CSD17309Q3 | DQG0008A | U$27, U$28 | | | | | | | | | | | | | | | | | CSD17309Q3 | | | | | | | | | | | | | | | | | | Texas Instruments
1 | EN11-HSM1BF20 | EN11-HSM1BF20 | EN11HSM1BF20 | S1 | ENCODER 11MM ROTARY SW TOP ADJ | | | EN11-HSM1BF20 | | | | | | ENCODER 11MM ROTARY SW TOP ADJ | | | | 26mm | | TT Electronics/BI Magnetics | EN11-HSM1BF20
1 | FT232RL-REEL | FT232RL-REEL | SOP65P780X200-28N | U2 | USB Full Speed to Serial UART IC, Includes Oscillator and EEPROM - SSOP-28 | | | | | | | | | | | | | | Future Technology Devices International Ltd
1 | LM317MBSTT3 | LM317MBSTT3 | SOT223 | IC8 | 500 mA Adjustable Output Positive Voltage Regulator | | | | | | | | | | | | | | | | | | | | | | | | | LM317M
1 | LSM9DS1 | LSM9DS1 | PQFN24P43_350X300X102L35X23N | U4 | iNEMO inertial module: 3D accelerometer, 3D gyroscope, 3D magnetometer | | | | | Unavailable | | | | iNEMO inertial module: 3D accelerometer, 3D gyroscope, 3D magnetometer | | | | | | | | STMicroelectronics | LSM9DS1 | | | | | | None | | None
1 | MBRS340T3 | MBRS340T3 | SMC | D1 | SCHOTTKY BARRIER RECTIFIER 3.0 AMPERES 20, 30, 40 VOLT
3 | Motor Coil A | SCREW-TERMINAL-GREEN(2P-5.0) | H2-5.0-10.5X8.0MM | J4, J10, J12 | 320110031 | | | | | | | | | | | | | | | | | | | | | | | | | | | | | | | | | GREEN-2P-5.0
3 | Motor Coil B | SCREW-TERMINAL-GREEN(2P-5.0) | H2-5.0-10.5X8.0MM | J3, J9, J11 | 320110031 | | | | | | | | | | | | | | | | | | | | | | | | | | | | | | | | | GREEN-2P-5.0
1 | OLED | OLED | SIP-20 | SCREEN1
1 | POWER_JACKPTH_BREAD | POWER_JACKPTH_BREAD | POWER_JACK_PTH_BREAD | J1 | Power Jack Connector | | | | | | | | | | | | | | | | | | | | | | | | | | | | PRT-10811
1 | S1315F8_RAW | S1315F8_RAW | S1315F8_SMT | IC1
1 | STEREOJACK | STEREOJACK | STX3100 | X1 | MIC/HEADPHONE JACK
1 | STM32F313VCT6 | STM32F313VCT6 | QFP50P1600X1600X160-100N | IC0
1 | TL3342F160QG | TL3342F160QG | SW_TL3342F160QG | S2 | TL3342 Series SPST 1.6 N Round Button Gull Wing Surface Mount Tactile Switch | | | | | | | | | | | | | | E SWITCH
1 | TPD8S300RUKRRUK0020B_NV | TPD8S300RUKRRUK0020B_NV | RUK0020B_NV | U1
3 | TPS54336ADRCR | TPS54336ADRCR | DRC0010J | U5, U6, U7
1 | TPS659821 | TPS659821 | QFN50P800X800X100-57N | U$29

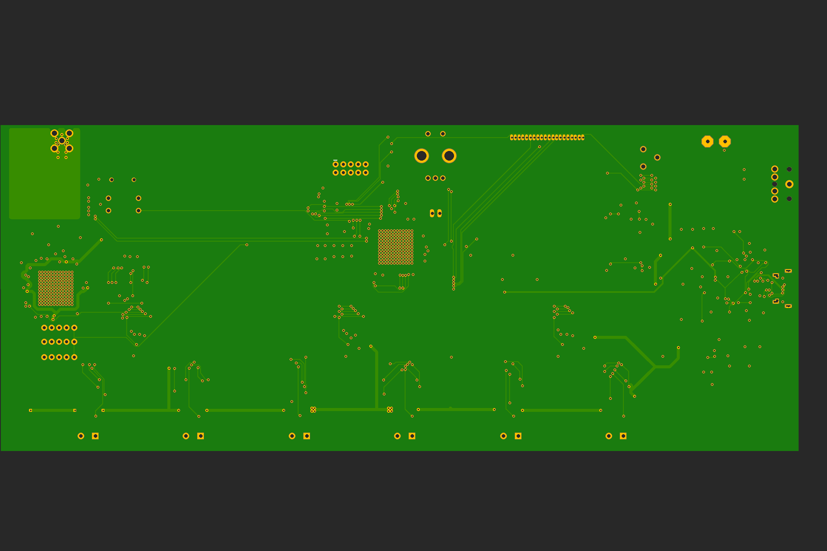
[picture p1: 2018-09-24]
hardware/main_smd_back.png

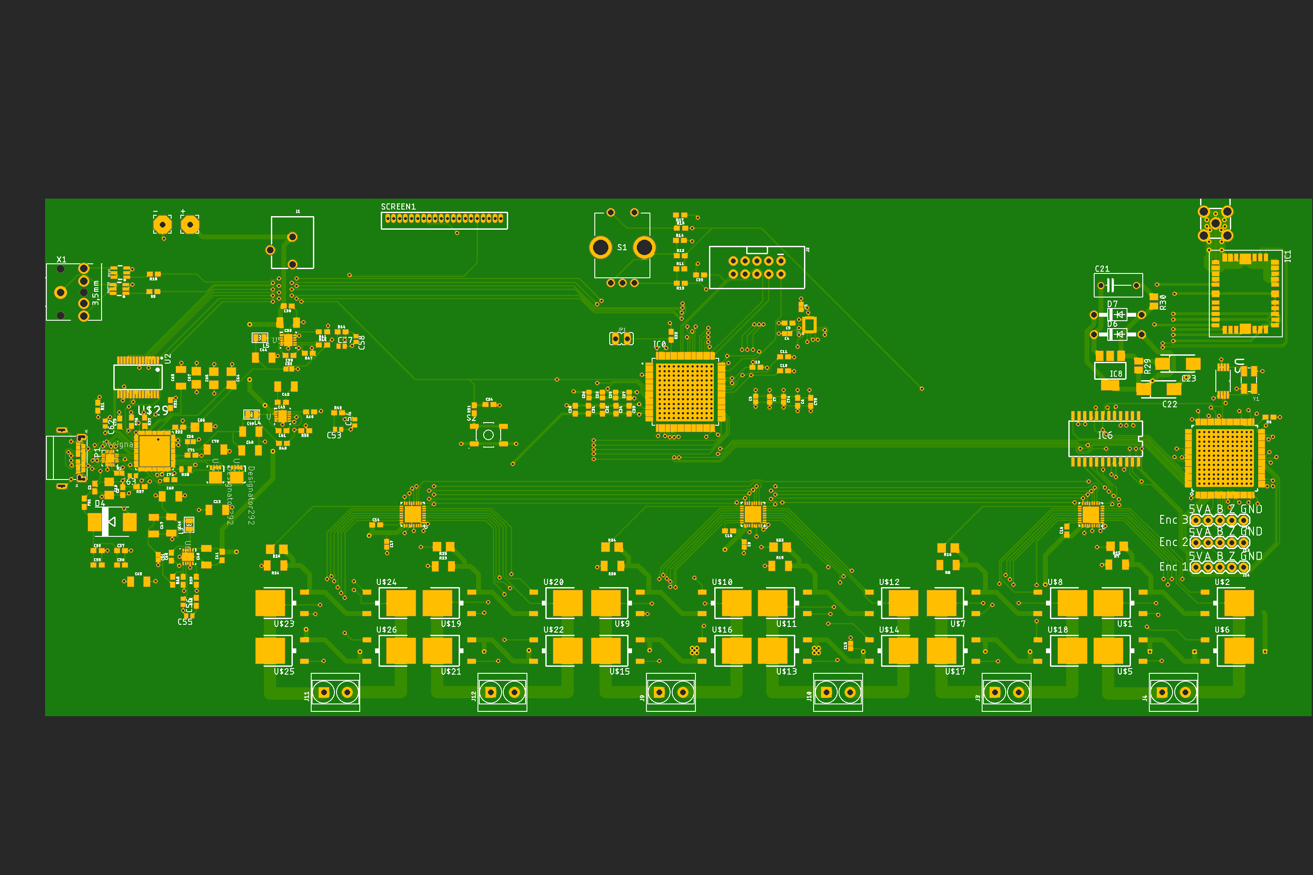
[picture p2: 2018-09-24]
hardware/main_smd.png

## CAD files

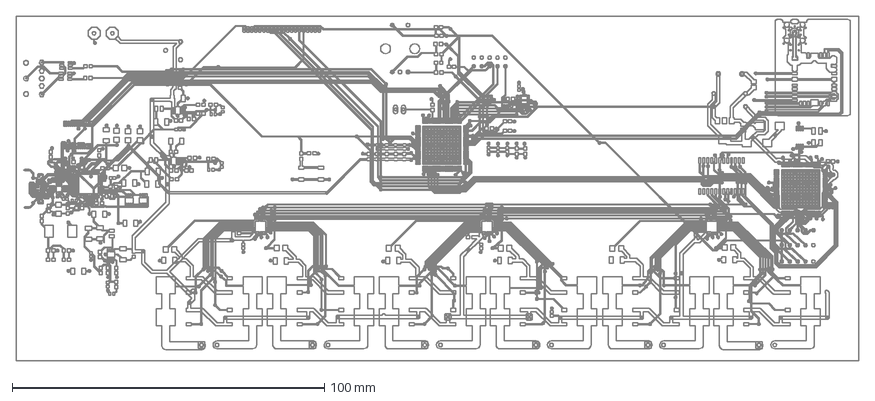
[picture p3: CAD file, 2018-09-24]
hardware/main_smd.dxf
269.8 x 110.3 mm

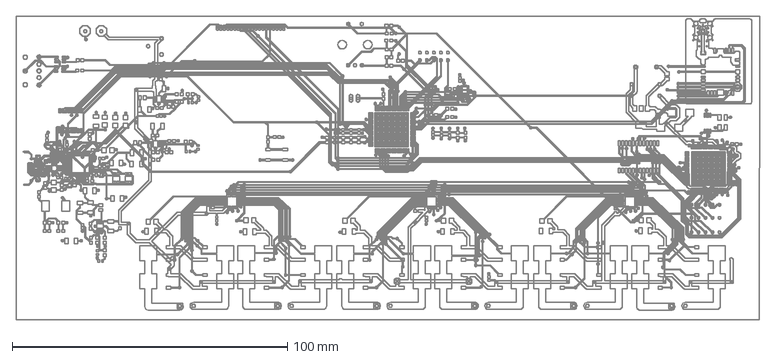
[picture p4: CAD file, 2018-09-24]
hardware/main_smd_back.dxf
269.8 x 110.3 mm

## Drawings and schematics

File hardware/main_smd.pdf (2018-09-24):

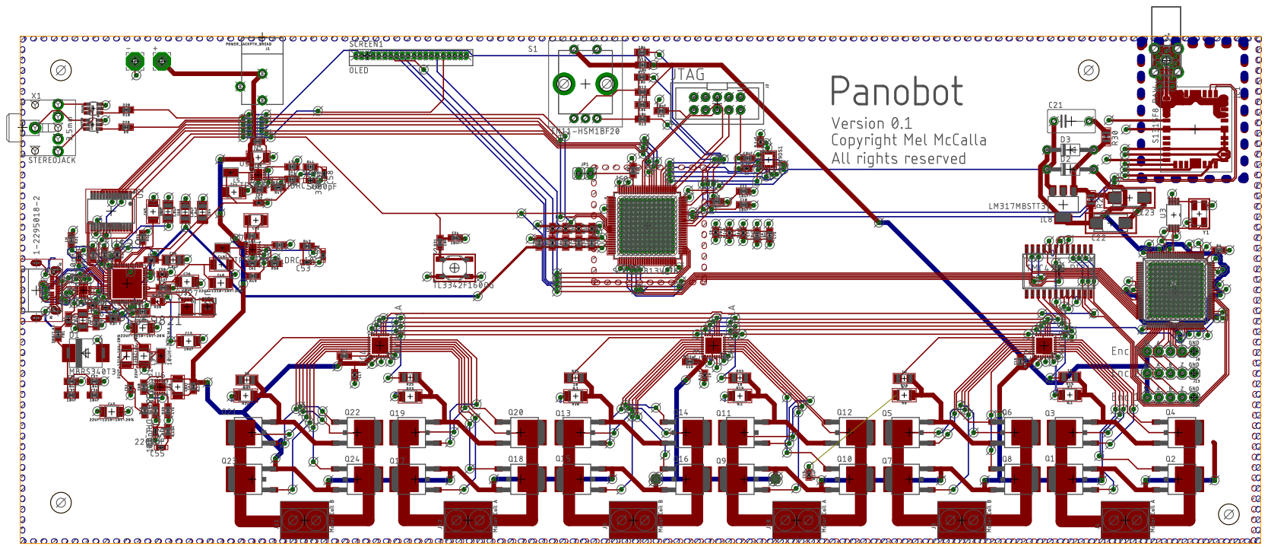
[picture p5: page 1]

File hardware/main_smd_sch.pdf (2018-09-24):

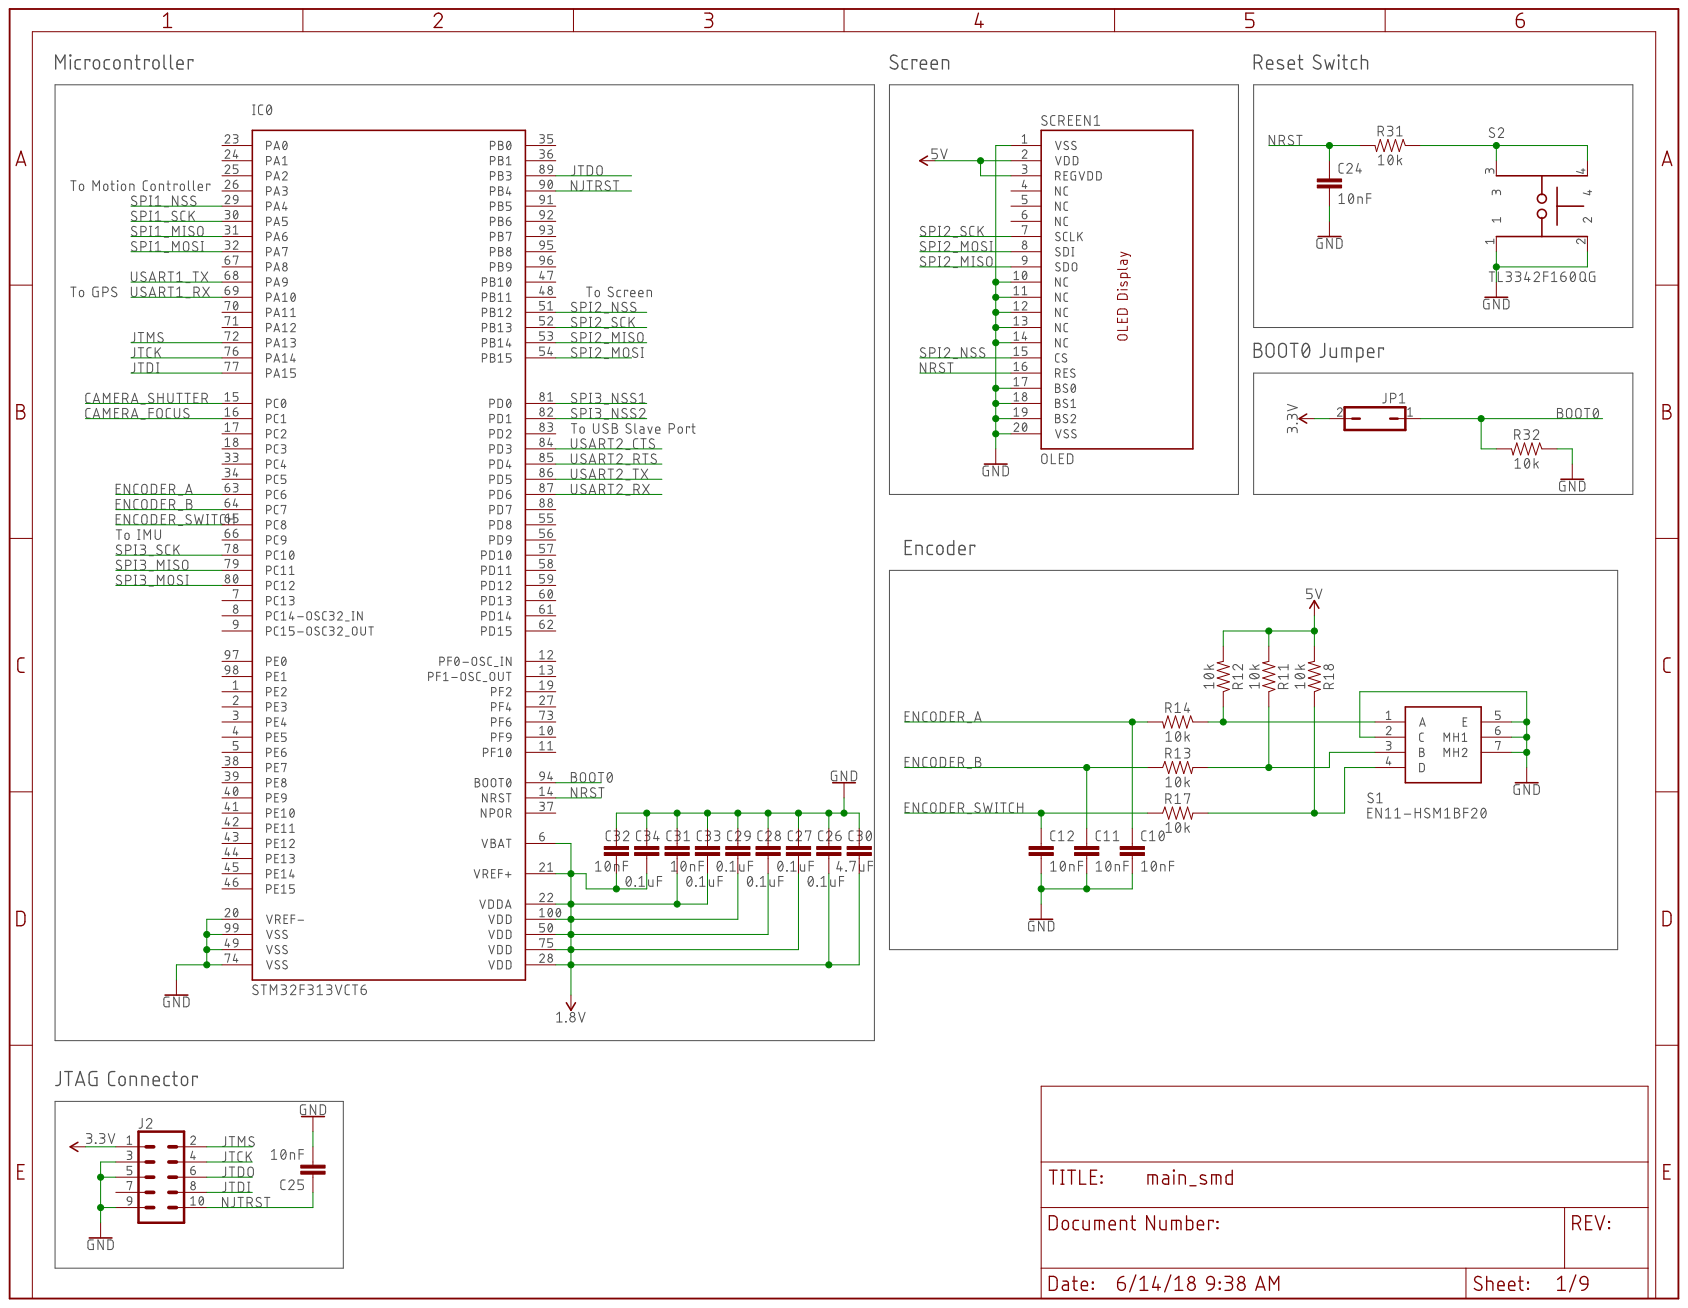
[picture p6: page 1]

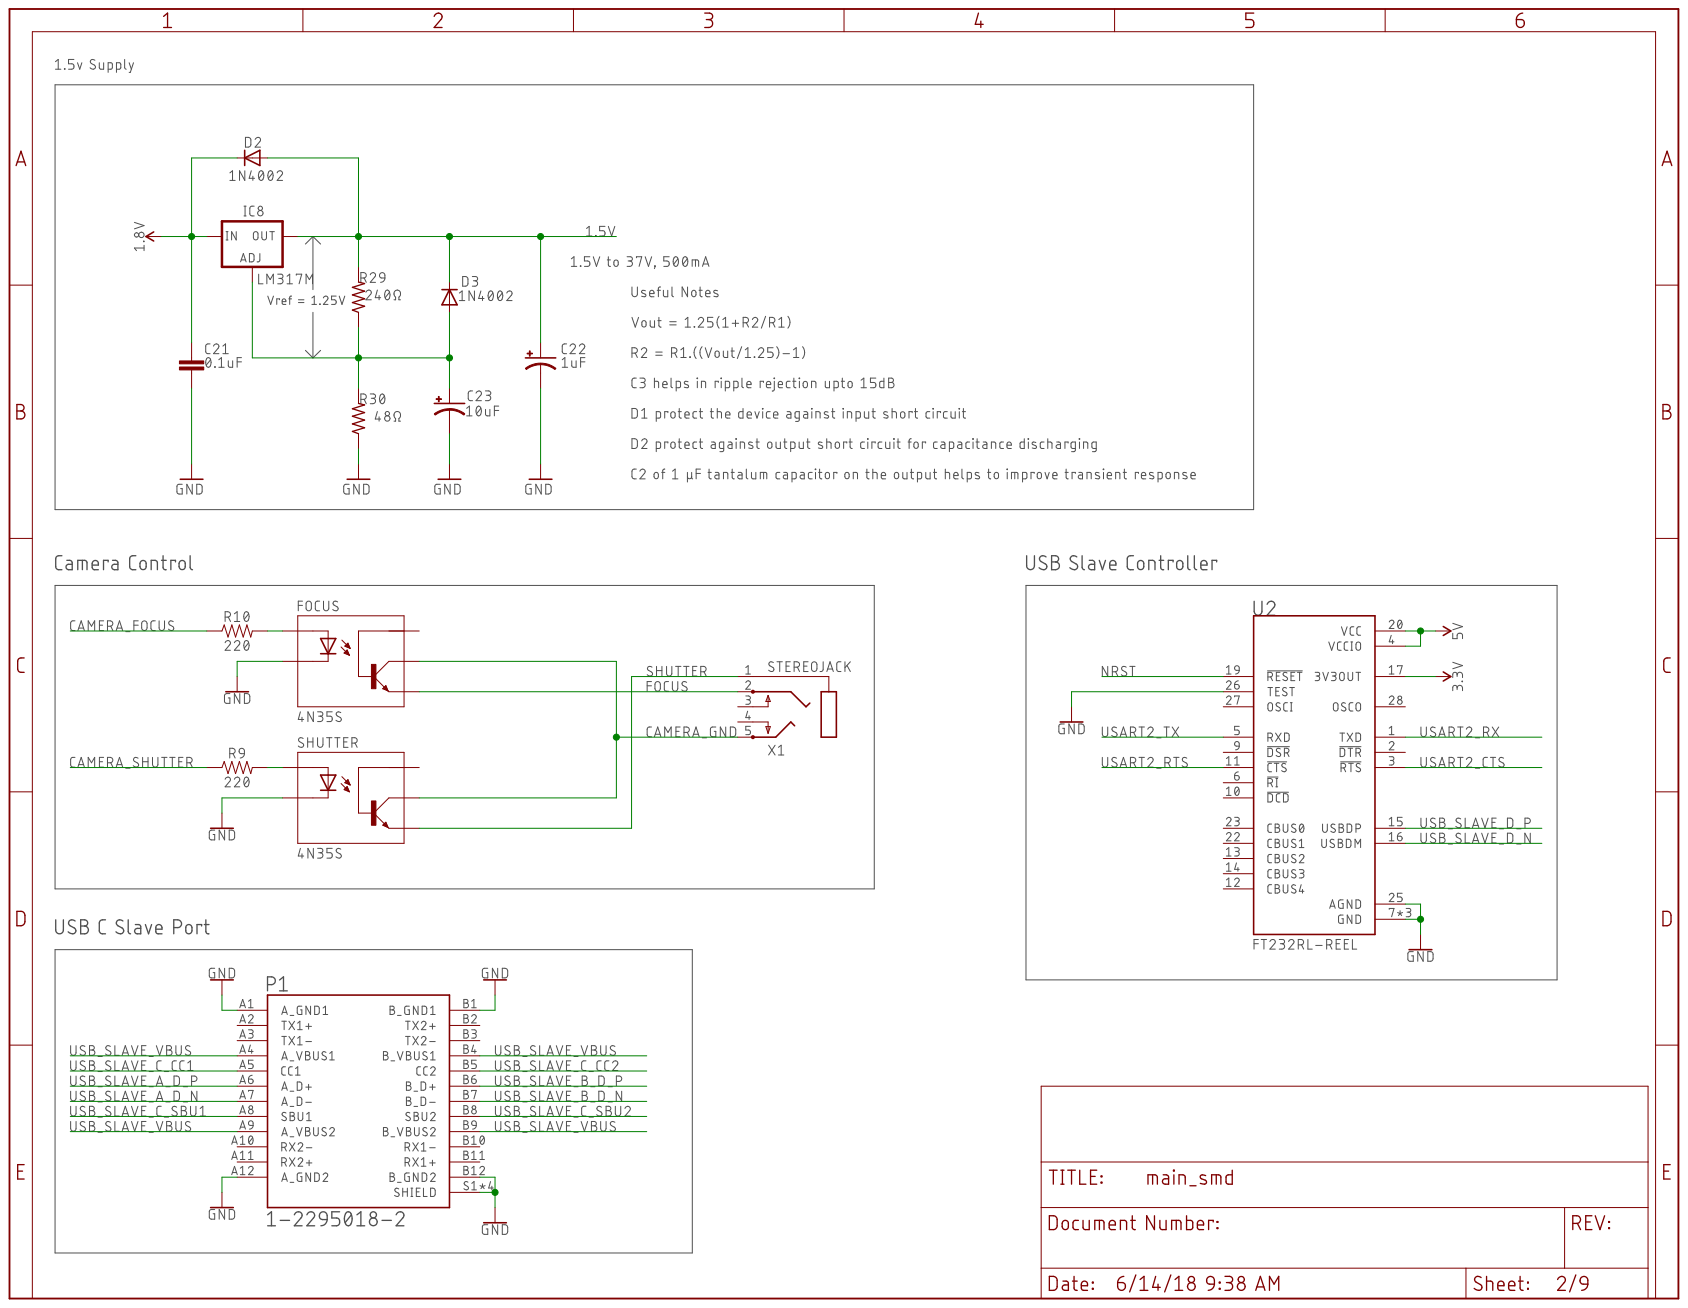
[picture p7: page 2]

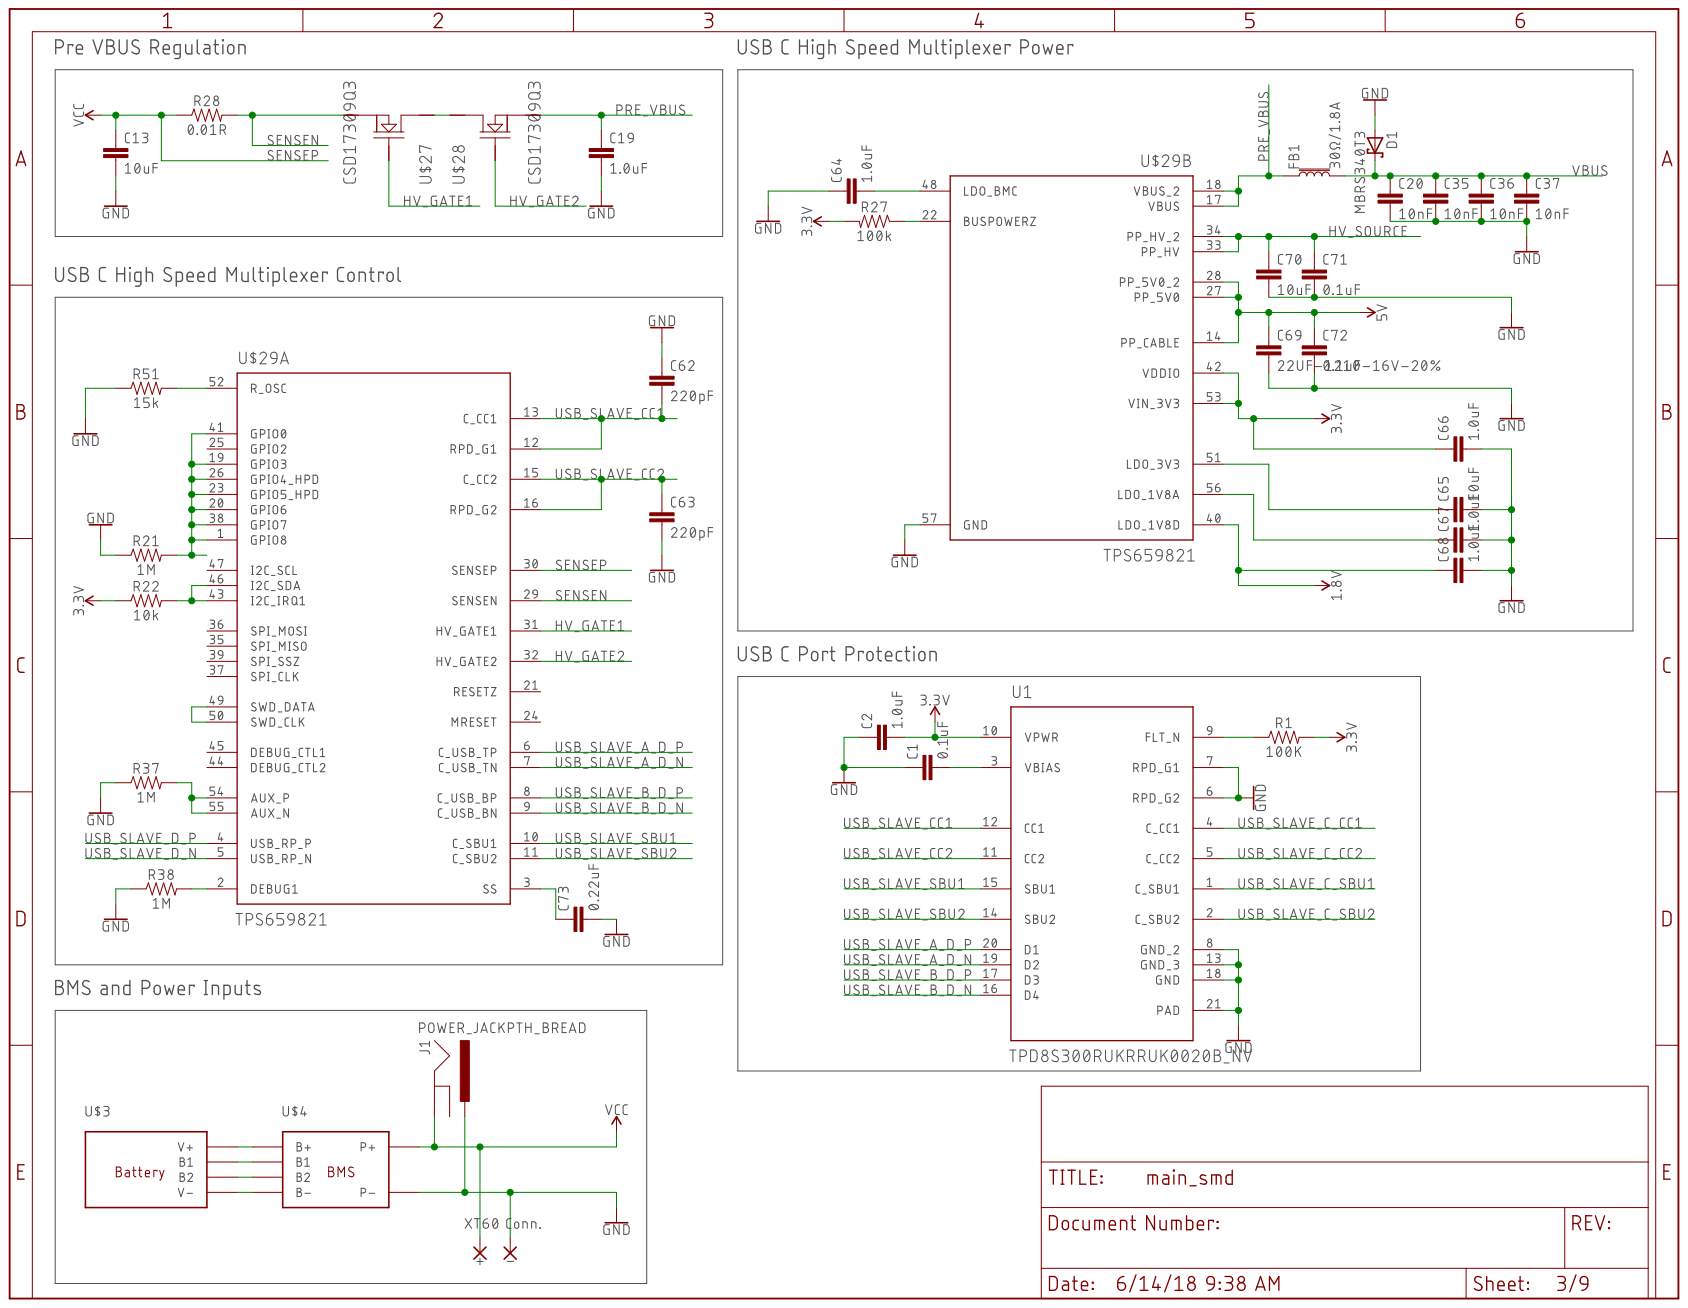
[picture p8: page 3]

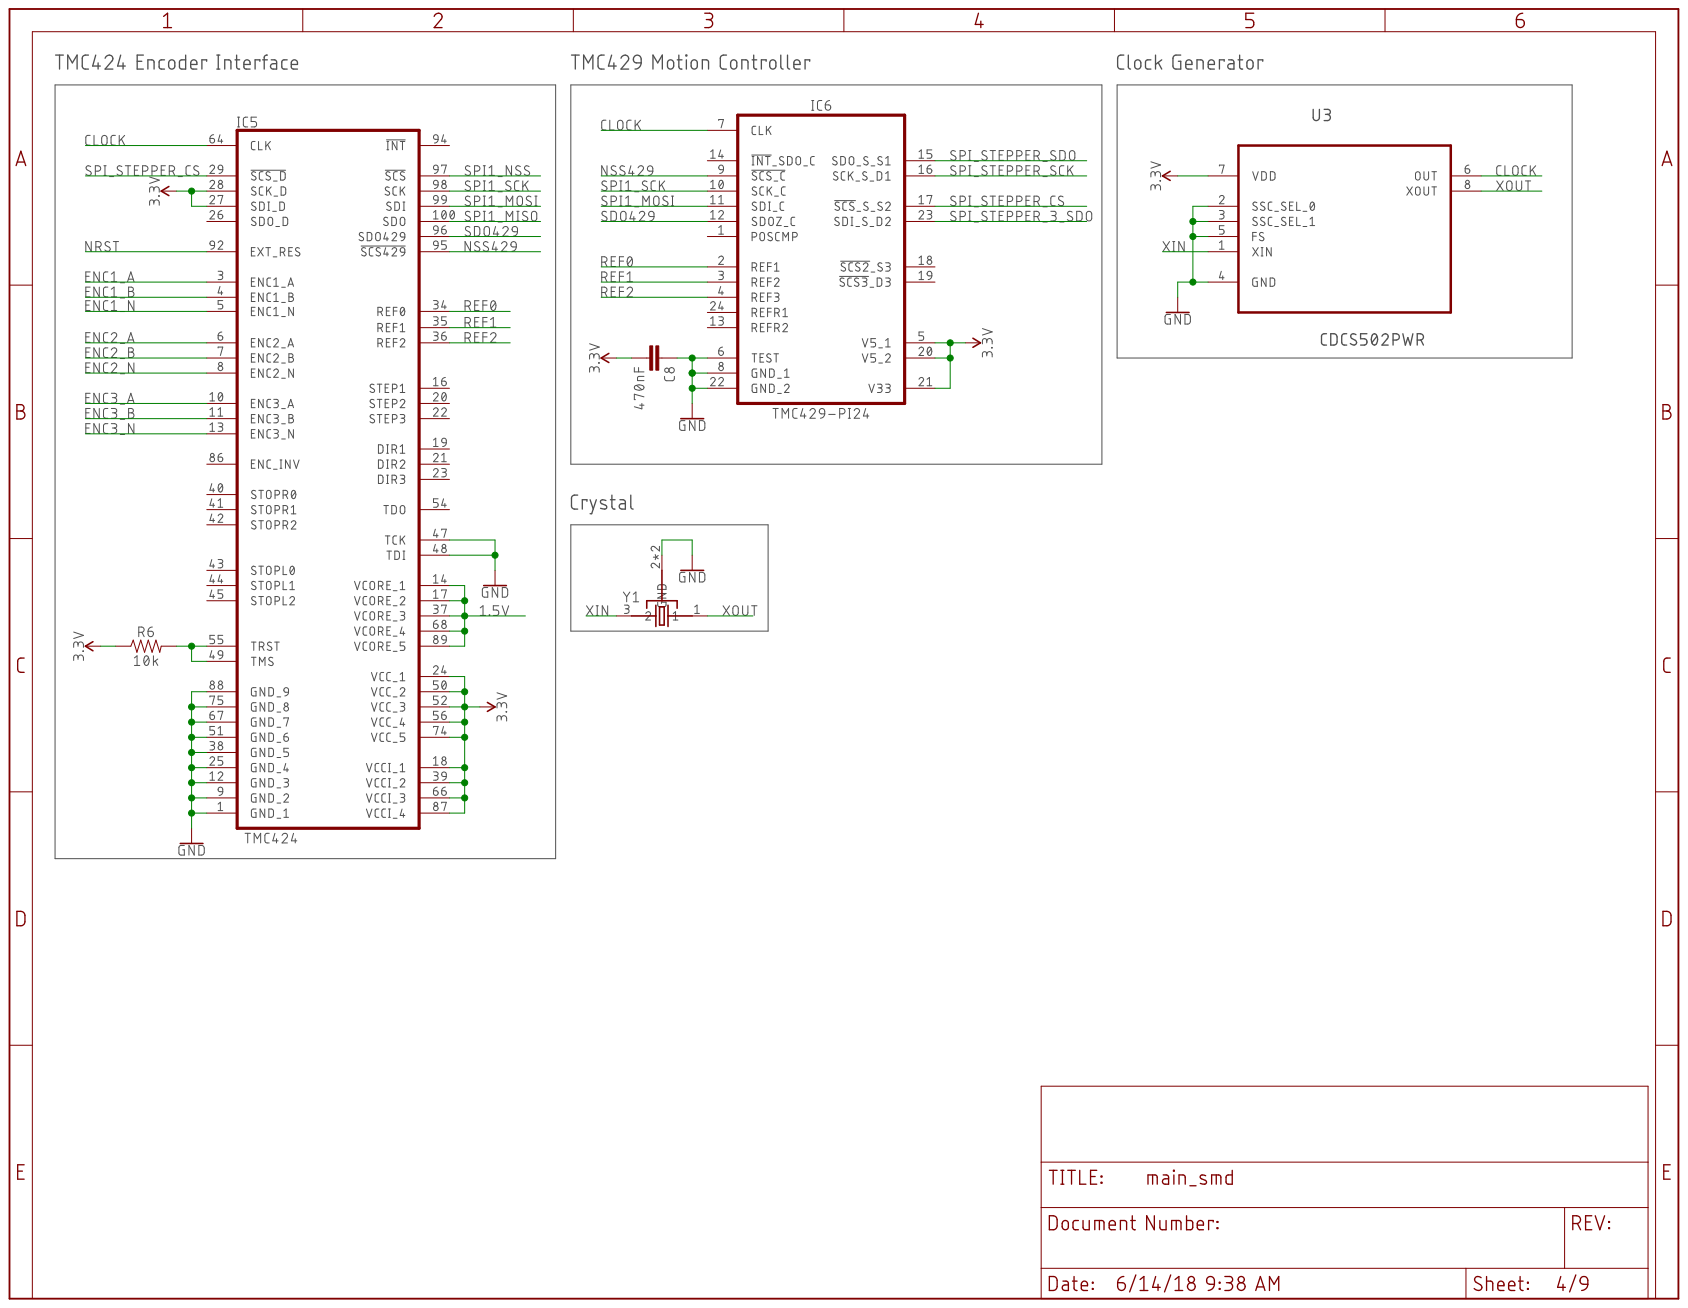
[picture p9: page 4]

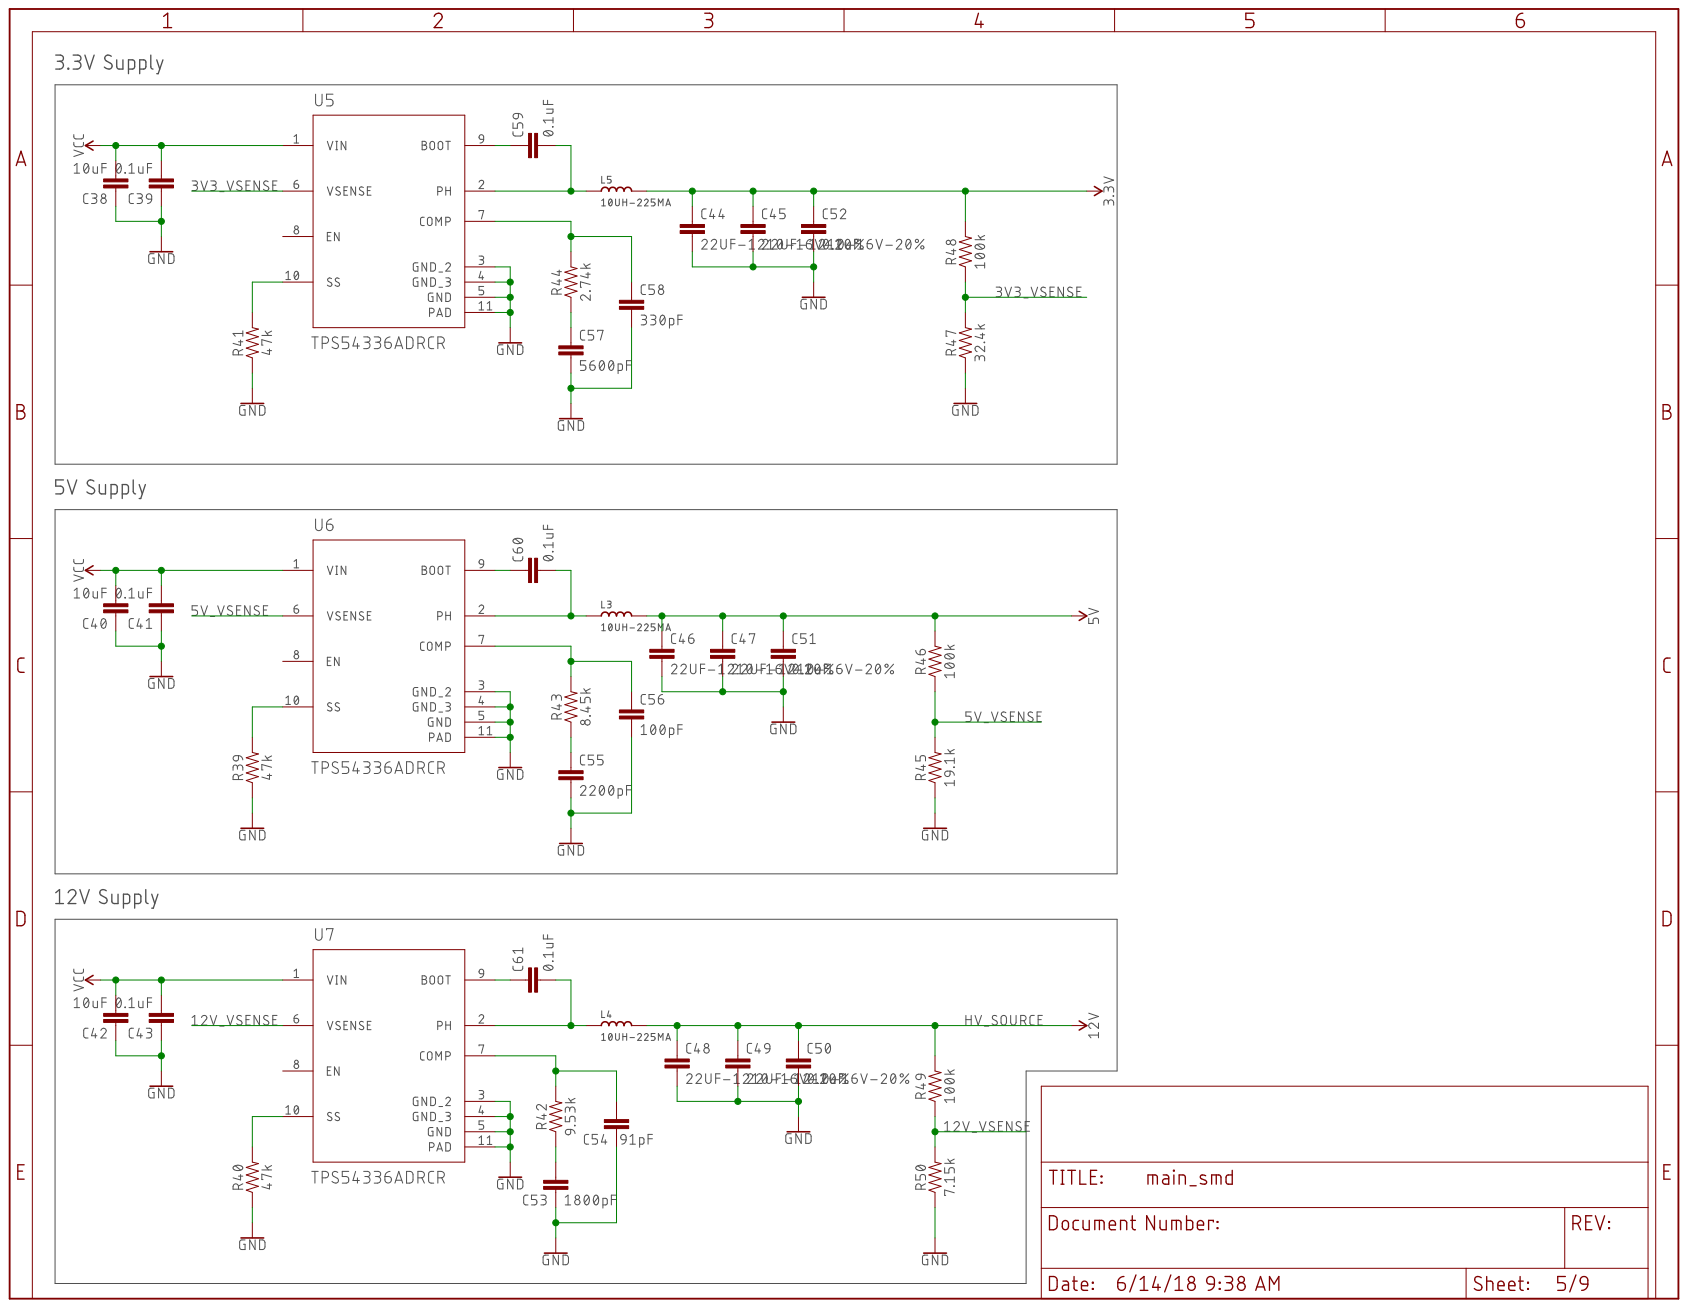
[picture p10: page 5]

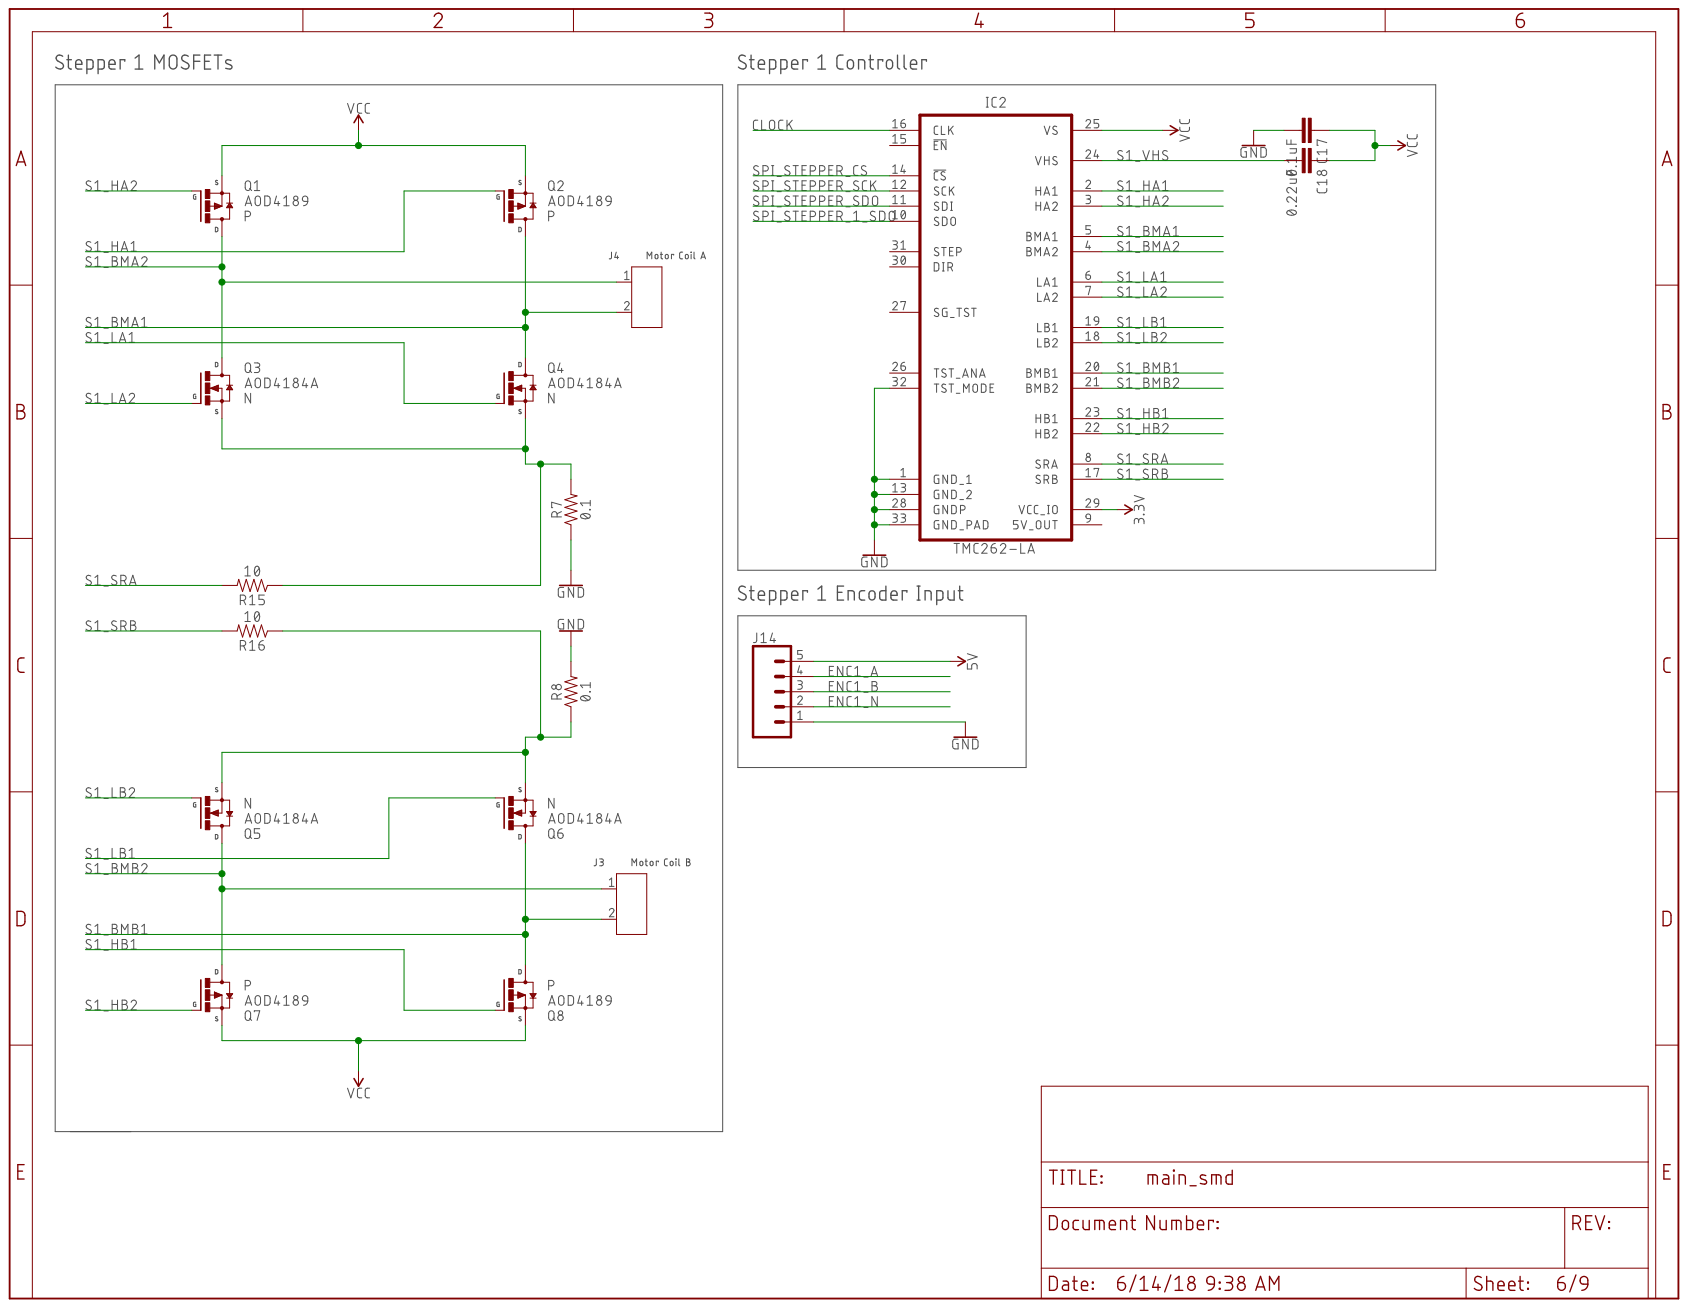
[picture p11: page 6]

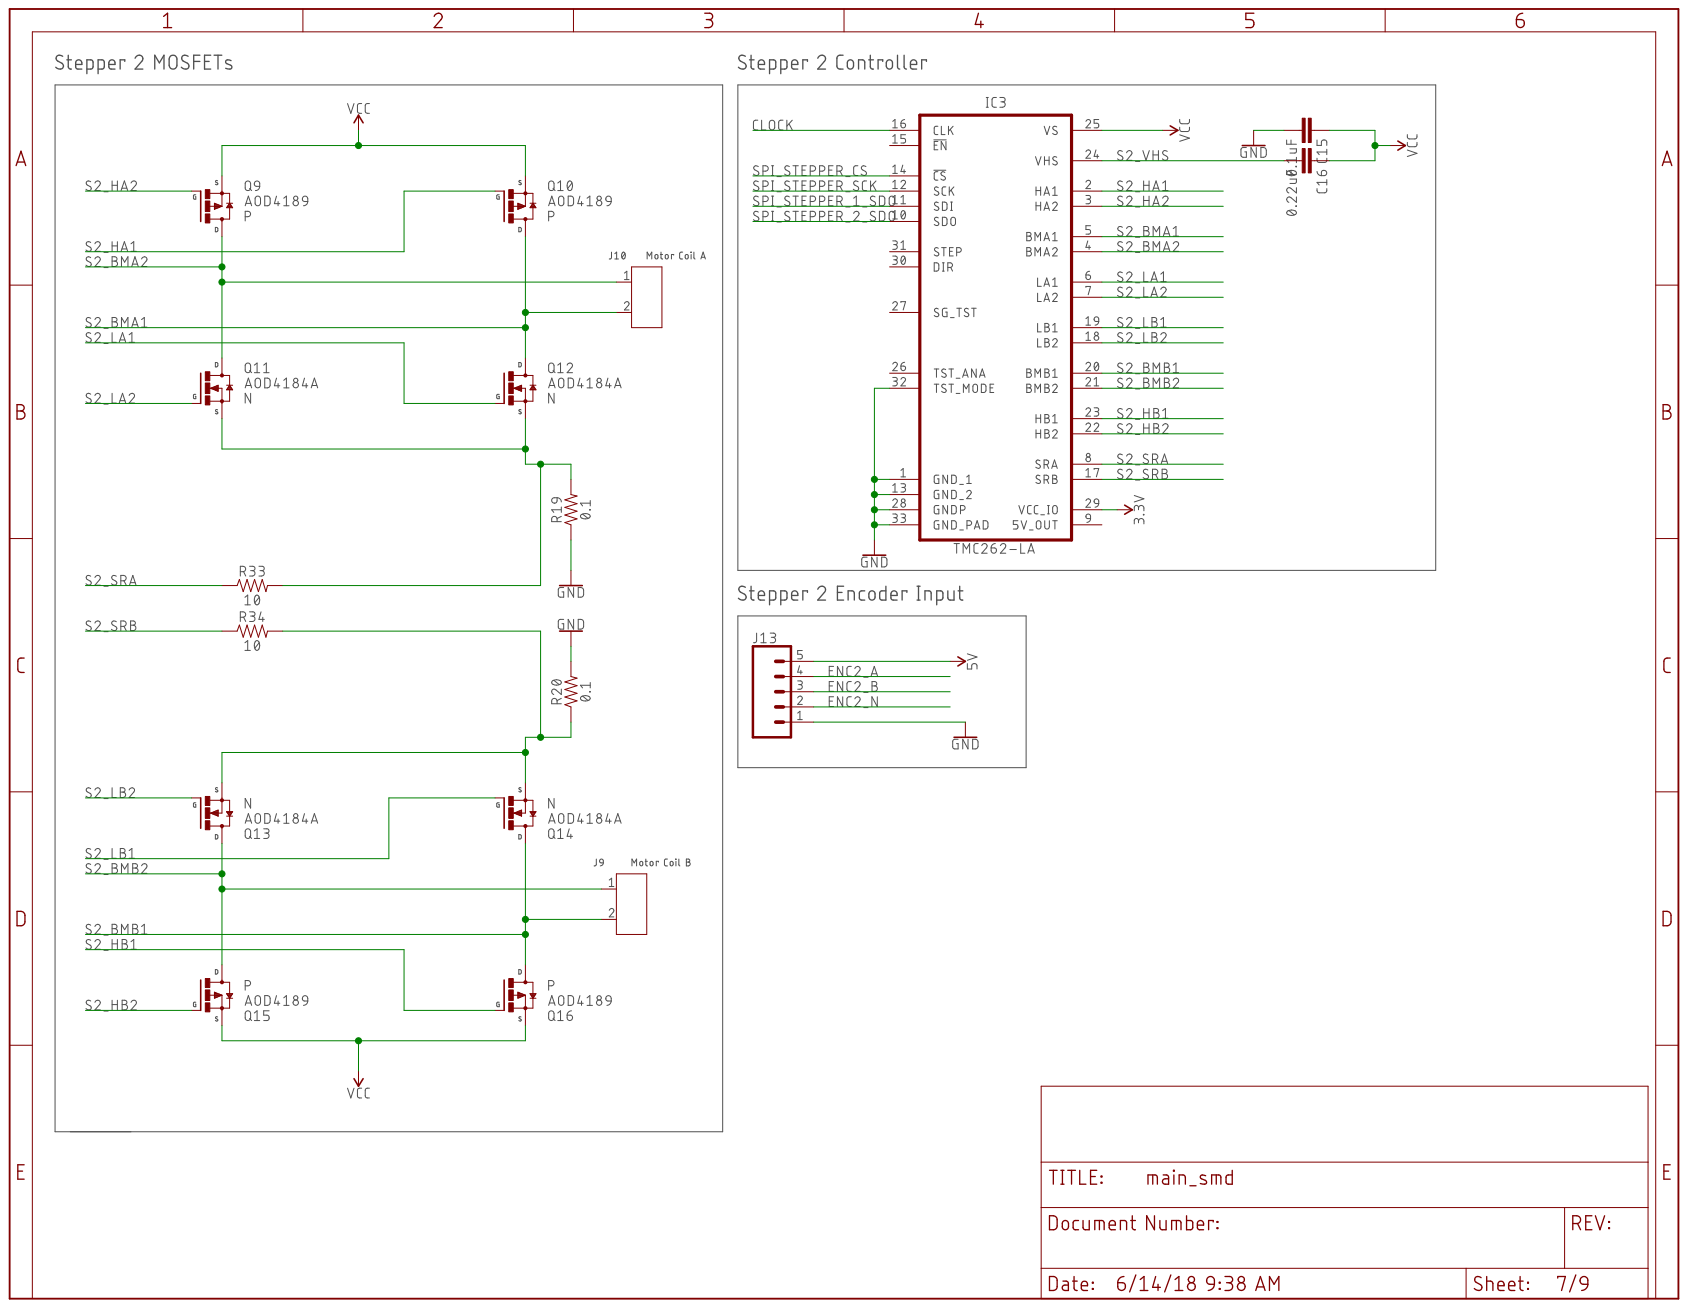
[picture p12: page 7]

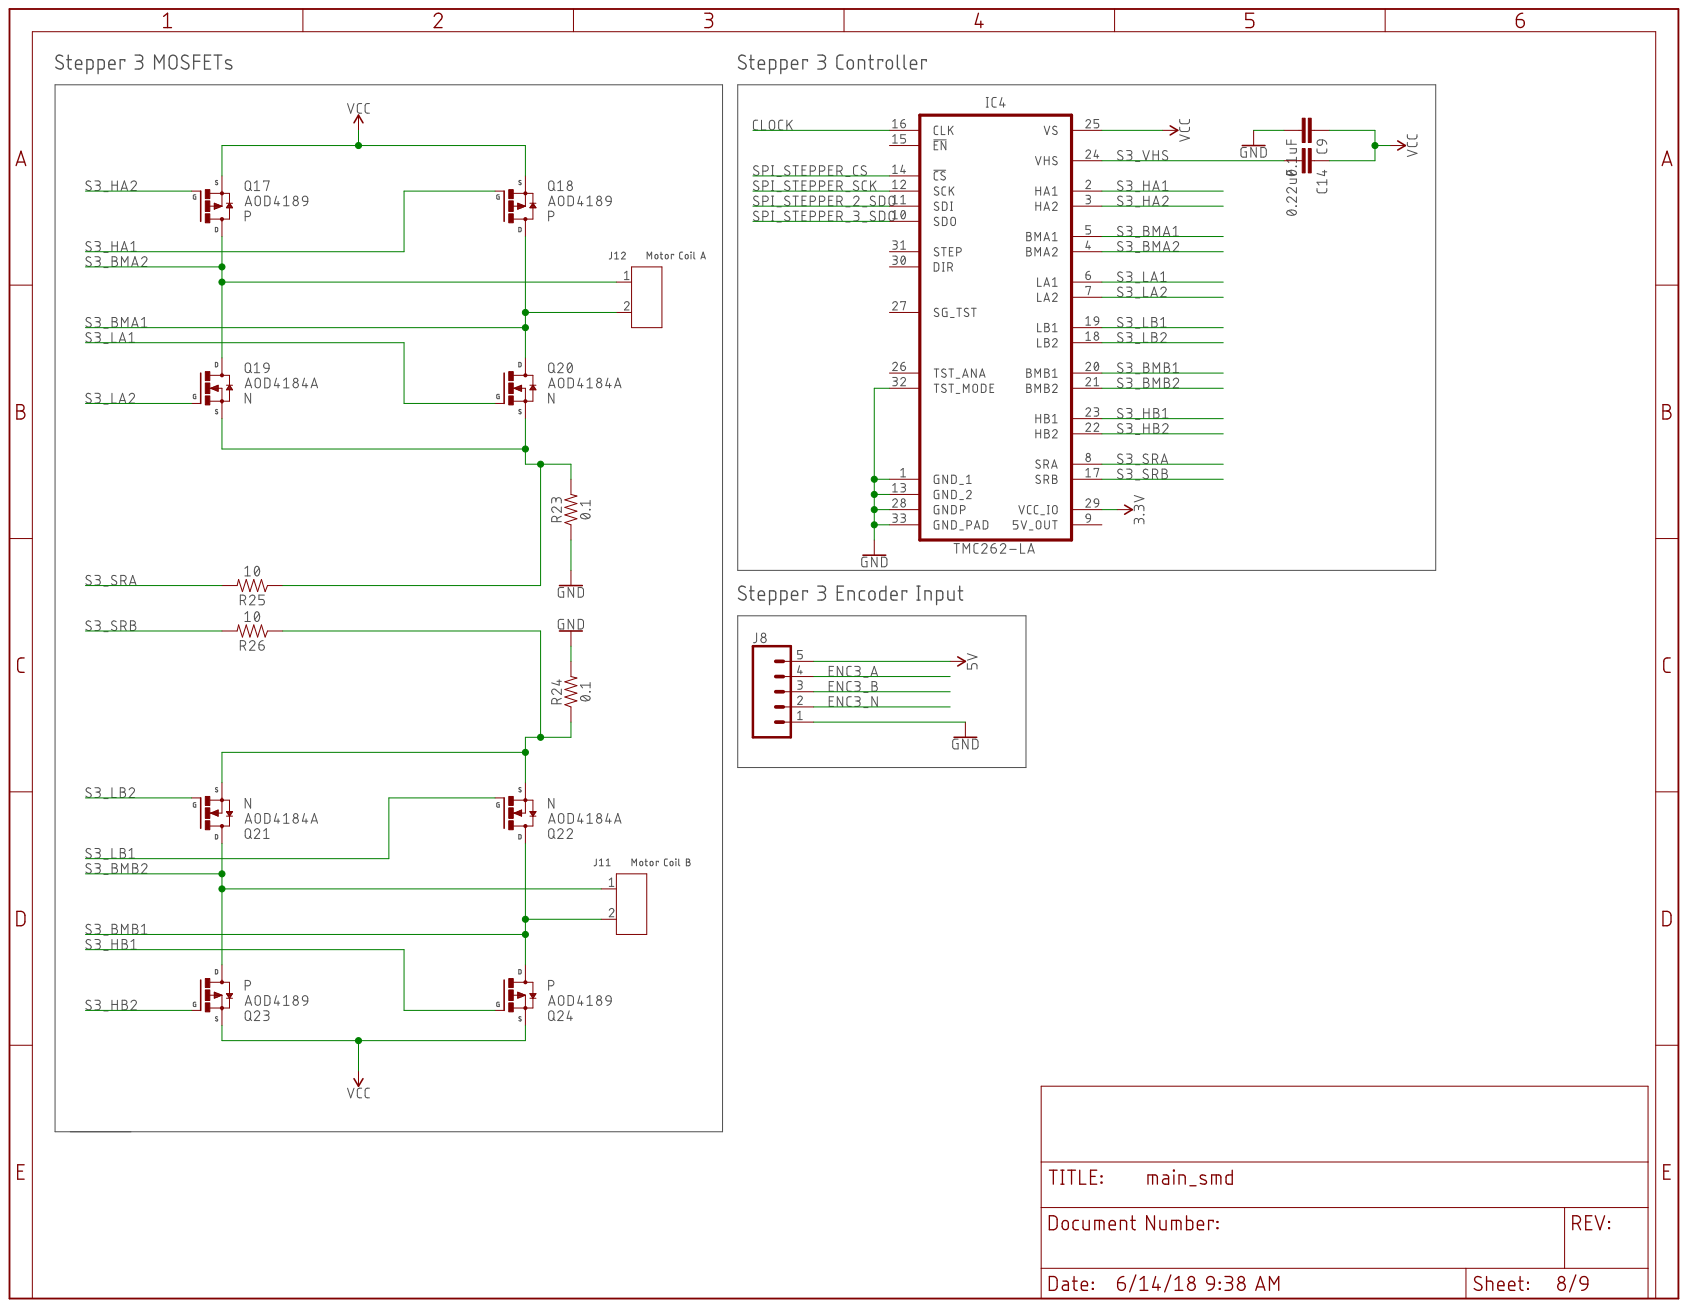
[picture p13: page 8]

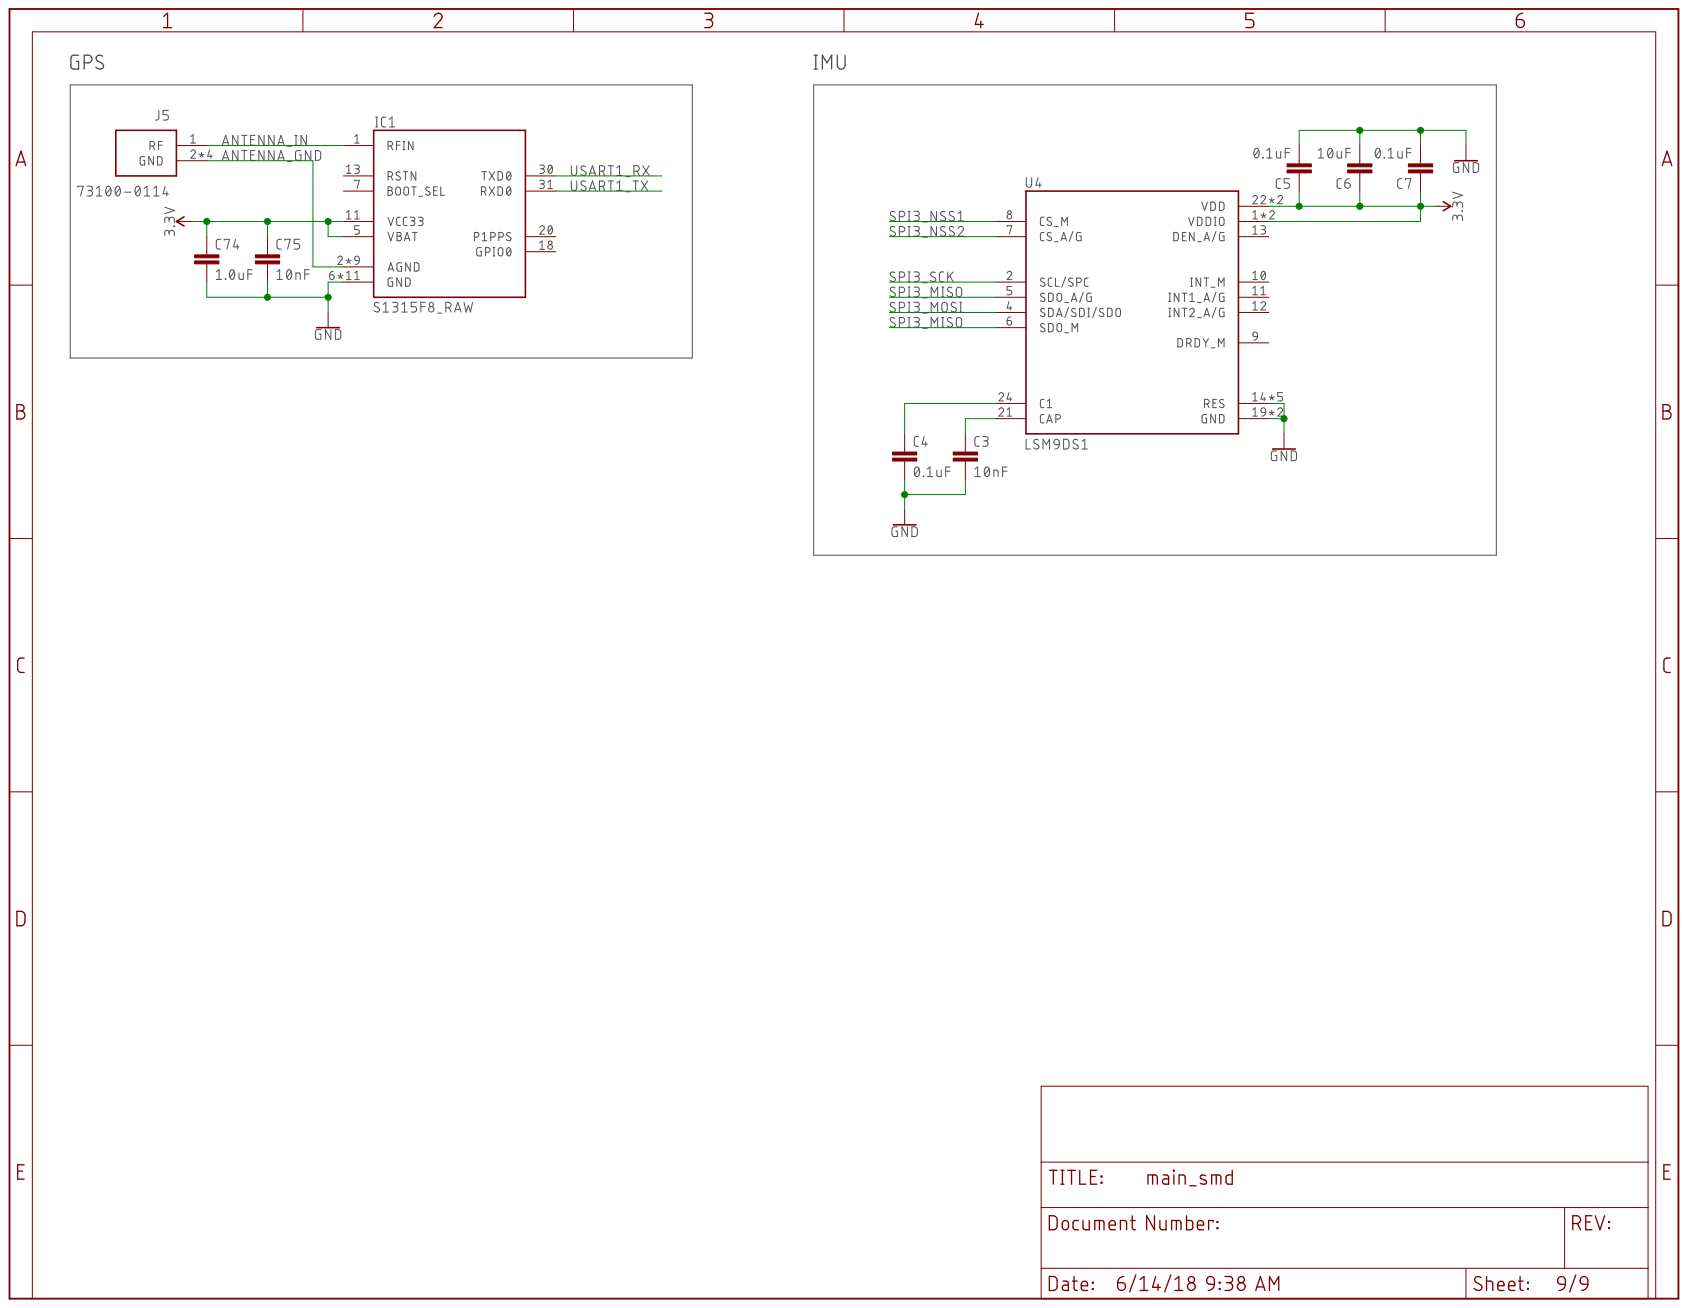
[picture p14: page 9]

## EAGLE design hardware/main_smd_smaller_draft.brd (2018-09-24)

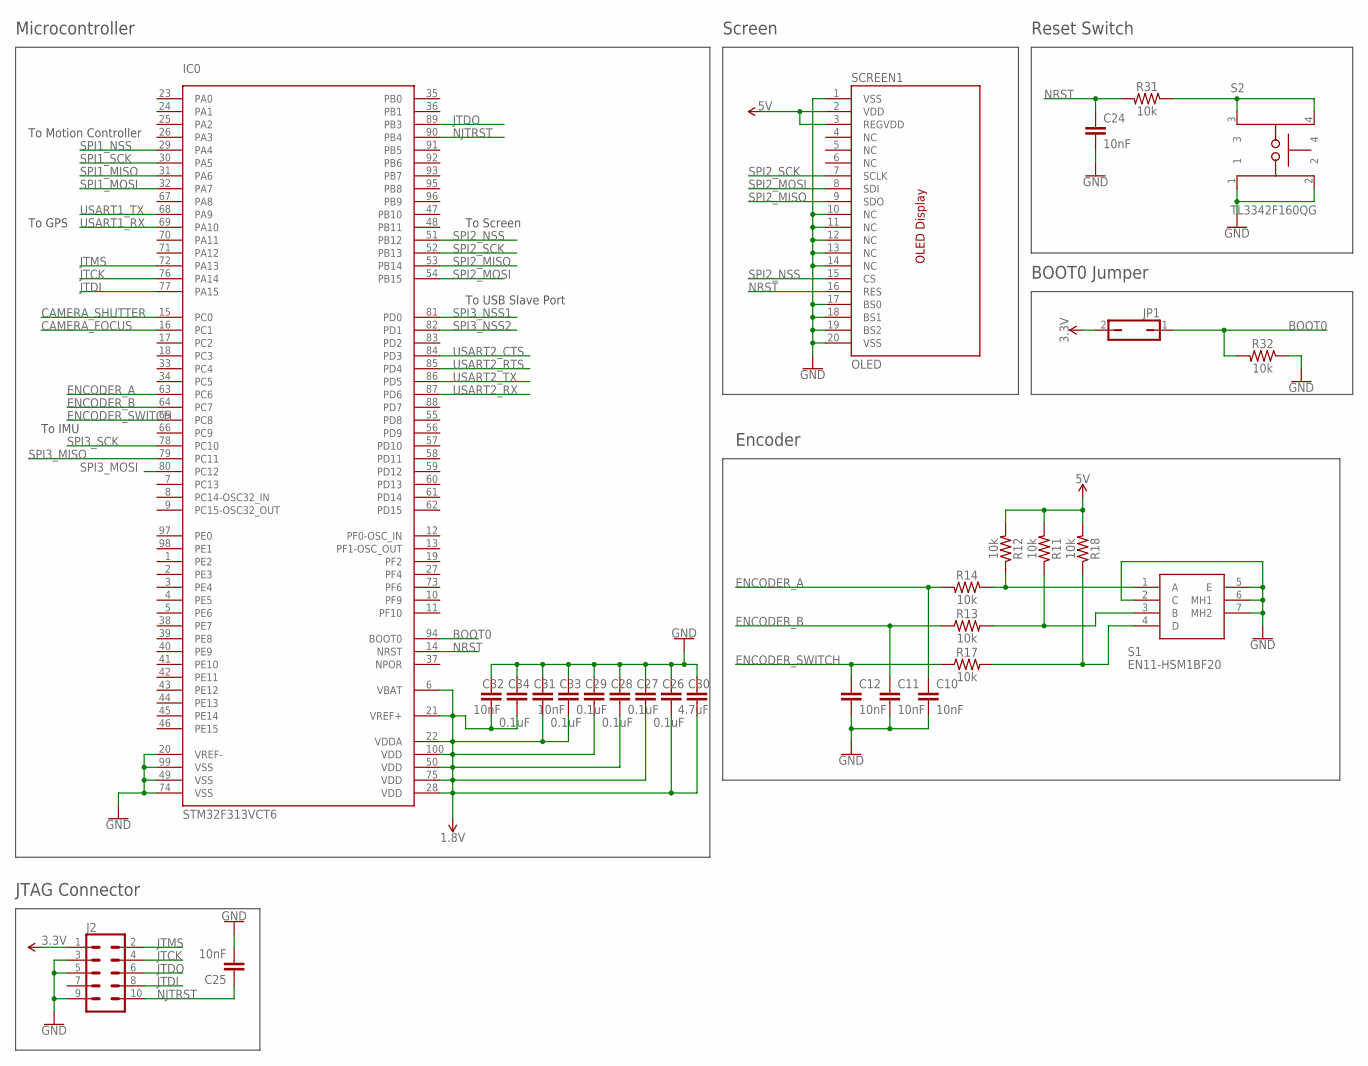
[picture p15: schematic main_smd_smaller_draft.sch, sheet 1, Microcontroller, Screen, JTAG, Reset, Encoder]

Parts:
C10, C11, C12, C24, C25, C31, C32: 10nF; 0603
C26, C27, C28, C29: 0.1uF; 0402
C30: 4.7uF; 0603
C33, C34: 0.1uF; 0603
IC0: STM32F313VCT6; QFP50P1600X1600X160-100N
J2: CONN_05X2SHD_LOCK; 2X5-SHROUDED_LOCK
JP1: JP1Q; JP1
R11, R12, R13, R14, R17, R18, R31, R32: 10k; 0603
S1: EN11-HSM1BF20; EN11HSM1BF20
S2: TL3342F160QG; SW_TL3342F160QG
SCREEN1: OLED; SIP-20

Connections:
1.8V: C26.1, C27.1, C28.1, C29.1, C30.1, C31.2, C32.2, C33.2, C34.2, IC0.6 (VBAT), IC0.21 (VREF+), IC0.22 (VDDA), IC0.28 (VDD), IC0.50 (VDD), IC0.75 (VDD), IC0.100 (VDD); also elsewhere on the board
3.3V: J2.1, JP1.2; also elsewhere on the board
5V: R11.2, R12.2, R18.2, SCREEN1.2 (VDD), SCREEN1.3 (REGVDD); also elsewhere on the board
BOOT0: IC0.94 (BOOT0), JP1.1, R32.2
CAMERA_FOCUS: IC0.16 (PC1); also elsewhere on the board
CAMERA_SHUTTER: IC0.15 (PC0); also elsewhere on the board
ENCODER_A: C10.1, IC0.63 (PC6), R14.2
ENCODER_B: C11.1, IC0.64 (PC7), R13.1
ENCODER_SWITCH: C12.1, IC0.65 (PC8), R17.1
GND: C10.2, C11.2, C12.2, C24.2, C25.2, C26.2, C27.2, C28.2, C29.2, C30.2, C31.1, C32.1, C33.1, C34.1, IC0.20 (VREF-), IC0.49 (VSS), IC0.74 (VSS), IC0.99 (VSS), J2.3, J2.5, J2.9, R32.1, S1.2 (C), S1.5 (E), S1.6 (MH1), S1.7 (MH2), S2.1, S2.2, SCREEN1.1 (VSS), SCREEN1.10 (NC), SCREEN1.11 (NC), SCREEN1.12 (NC), SCREEN1.13 (NC), SCREEN1.14 (NC), SCREEN1.17 (BS0), SCREEN1.18 (BS1), SCREEN1.19 (BS2), SCREEN1.20 (VSS); also elsewhere on the board
JTCK: IC0.76 (PA14), J2.4
JTDI: IC0.77 (PA15), J2.8
JTDO: IC0.89 (PB3), J2.6
JTMS: IC0.72 (PA13), J2.2
unnamed: R17.2, R18.1, S1.4 (D)
unnamed: R12.1, R14.1, S1.1 (A)
unnamed: R11.1, R13.2, S1.3 (B)
unnamed: R31.1, S2.3, S2.4
NJTRST: C25.1, IC0.90 (PB4), J2.10
NRST: C24.1, IC0.14 (NRST), R31.2, SCREEN1.16 (RES); also elsewhere on the board
SPI1_MISO: IC0.31 (PA6); also elsewhere on the board
SPI1_MOSI: IC0.32 (PA7); also elsewhere on the board
SPI1_NSS: IC0.29 (PA4); also elsewhere on the board
SPI1_SCK: IC0.30 (PA5); also elsewhere on the board
SPI2_MISO: IC0.53 (PB14), SCREEN1.9 (SDO)
SPI2_MOSI: IC0.54 (PB15), SCREEN1.8 (SDI)
SPI2_NSS: IC0.51 (PB12), SCREEN1.15 (CS)
SPI2_SCK: IC0.52 (PB13), SCREEN1.7 (SCLK)
SPI3_MISO: IC0.79 (PC11); also elsewhere on the board
SPI3_MOSI: IC0.80 (PC12); also elsewhere on the board
SPI3_NSS1: IC0.81 (PD0); also elsewhere on the board
SPI3_NSS2: IC0.82 (PD1); also elsewhere on the board
SPI3_SCK: IC0.78 (PC10); also elsewhere on the board
USART1_RX: IC0.69 (PA10); also elsewhere on the board
USART1_TX: IC0.68 (PA9); also elsewhere on the board
USART2_CTS: IC0.84 (PD3); also elsewhere on the board
USART2_RTS: IC0.85 (PD4); also elsewhere on the board
USART2_RX: IC0.87 (PD6); also elsewhere on the board
USART2_TX: IC0.86 (PD5); also elsewhere on the board

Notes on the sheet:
JTAG Connector
Microcontroller
Screen
Encoder
Reset Switch
BOOT0 Jumper
To Screen
To Motion Controller
To USB Slave Port
To GPS
To IMU

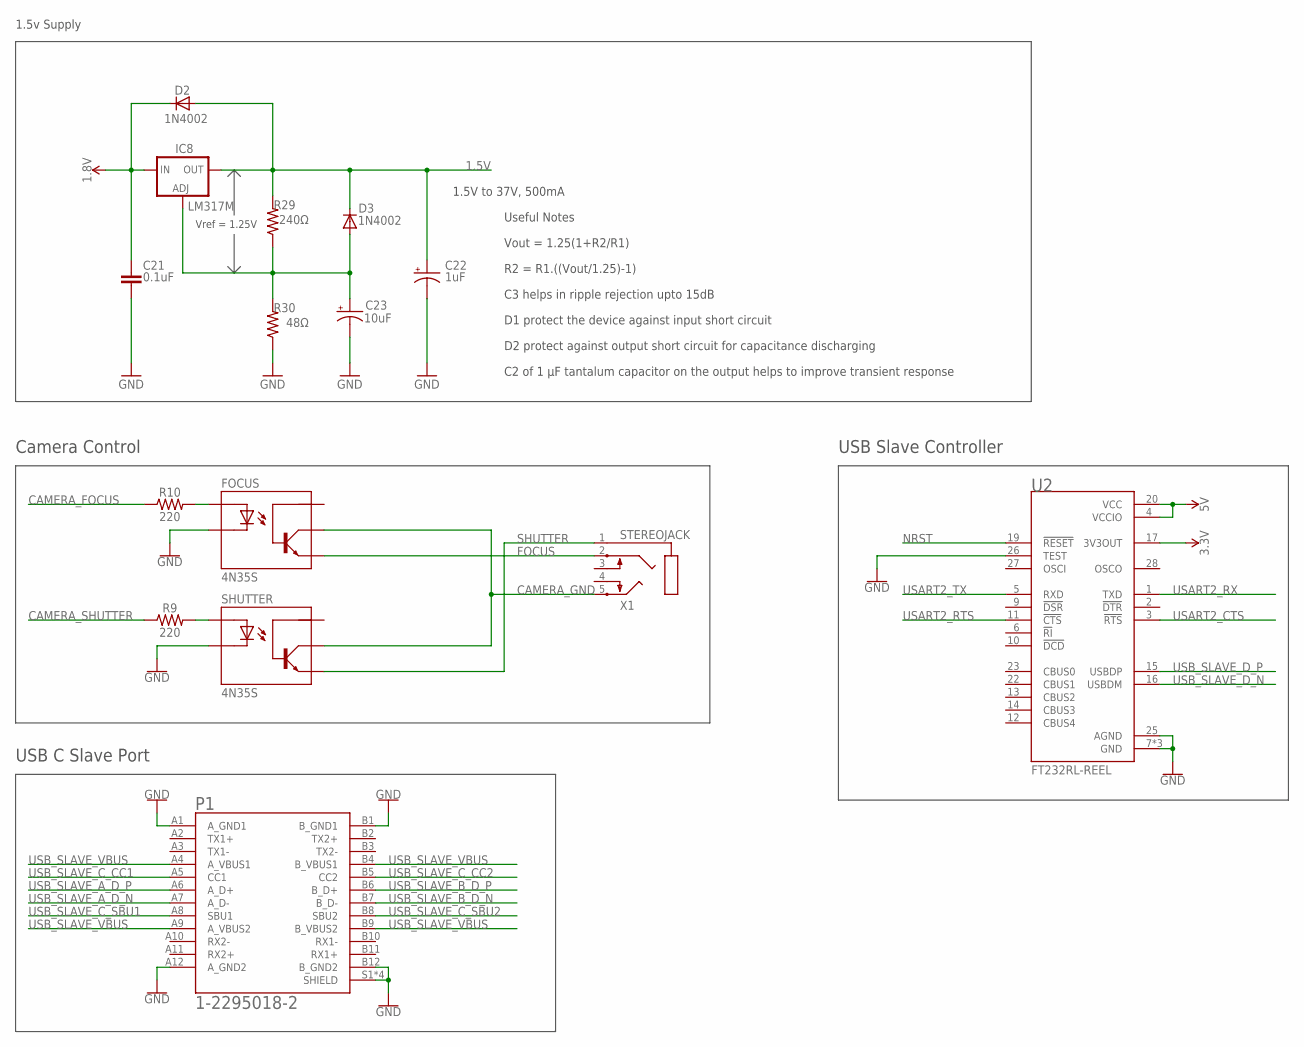
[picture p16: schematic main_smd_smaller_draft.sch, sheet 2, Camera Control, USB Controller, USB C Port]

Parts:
C21: 0.1uF; C075-052X106
C22: 1uF; 085CS_1AR
C23: 10uF; 085CS_1AR
D2, D3: 1N4002; DO41-10
FOCUS: 4N35S; SOT23-6
IC8: LM317MBSTT3; SOT223; PARTNUMBER LM317M
P1: 1-2295018-2; TE_1-2295018-2
R9, R10: 220; 0603
R29: 240Ω; M0805
R30: 48Ω; M0805
SHUTTER: 4N35S; SOT23-6
U2: FT232RL-REEL; SOP65P780X200-28N
X1: STEREOJACK; STX3100

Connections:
1.5V: C22.+, D2.A, D3.C, IC8.4 (OUT), R29.2; also elsewhere on the board
1.8V: C21.1, D2.C, IC8.3 (IN); also elsewhere on the board
3.3V: U2.17 (3V3OUT); also elsewhere on the board
5V: U2.4 (VCCIO), U2.20 (VCC); also elsewhere on the board
CAMERA_FOCUS: R10.1; also elsewhere on the board
CAMERA_GND: FOCUS.5, SHUTTER.5, X1.5
CAMERA_SHUTTER: R9.1; also elsewhere on the board
FOCUS: FOCUS.4, X1.2
GND: C21.2, C22.-, C23.-, FOCUS.2, P1.A1 (A_GND1), P1.A12 (A_GND2), P1.B1 (B_GND1), P1.B12 (B_GND2), P1.S1 (SHIELD), P1.S2 (SHIELD), P1.S3 (SHIELD), P1.S4 (SHIELD), R30.1, SHUTTER.2, U2.7 (GND), U2.18 (GND), U2.21 (GND), U2.25 (AGND), U2.26 (TEST); also elsewhere on the board
unnamed: FOCUS.1, R10.2
unnamed: R9.2, SHUTTER.1
unnamed: C23.+, D3.A, IC8.1 (ADJ), R29.1, R30.2
NRST: U2.19 (!RESET); also elsewhere on the board
SHUTTER: SHUTTER.4, X1.1
USART2_CTS: U2.3 (!RTS); also elsewhere on the board
USART2_RTS: U2.11 (!CTS); also elsewhere on the board
USART2_RX: U2.1 (TXD); also elsewhere on the board
USART2_TX: U2.5 (RXD); also elsewhere on the board
USB_SLAVE_A_D_N: P1.A7 (A_D-); also elsewhere on the board
USB_SLAVE_A_D_P: P1.A6 (A_D+); also elsewhere on the board
USB_SLAVE_B_D_N: P1.B7 (B_D-); also elsewhere on the board
USB_SLAVE_B_D_P: P1.B6 (B_D+); also elsewhere on the board
USB_SLAVE_C_CC1: P1.A5 (CC1); also elsewhere on the board
USB_SLAVE_C_CC2: P1.B5 (CC2); also elsewhere on the board
USB_SLAVE_C_SBU1: P1.A8 (SBU1); also elsewhere on the board
USB_SLAVE_C_SBU2: P1.B8 (SBU2); also elsewhere on the board
USB_SLAVE_D_N: U2.16 (USBDM); also elsewhere on the board
USB_SLAVE_D_P: U2.15 (USBDP); also elsewhere on the board
USB_SLAVE_VBUS: P1.A4 (A_VBUS1), P1.A9 (A_VBUS2), P1.B4 (B_VBUS1), P1.B9 (B_VBUS2)

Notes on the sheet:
C3 helps in ripple rejection upto 15dB
D1 protect the device against input short circuit
D2 protect against output short circuit for capacitance discharging
C2 of 1 µF tantalum capacitor on the output helps to improve transient response
Useful Notes
Vref = 1.25V
R2 = R1.((Vout/1.25)-1)
Vout = 1.25(1+R2/R1)
1.5V to 37V, 500mA
1.5v Supply
USB Slave Controller
Camera Control
USB C Slave Port

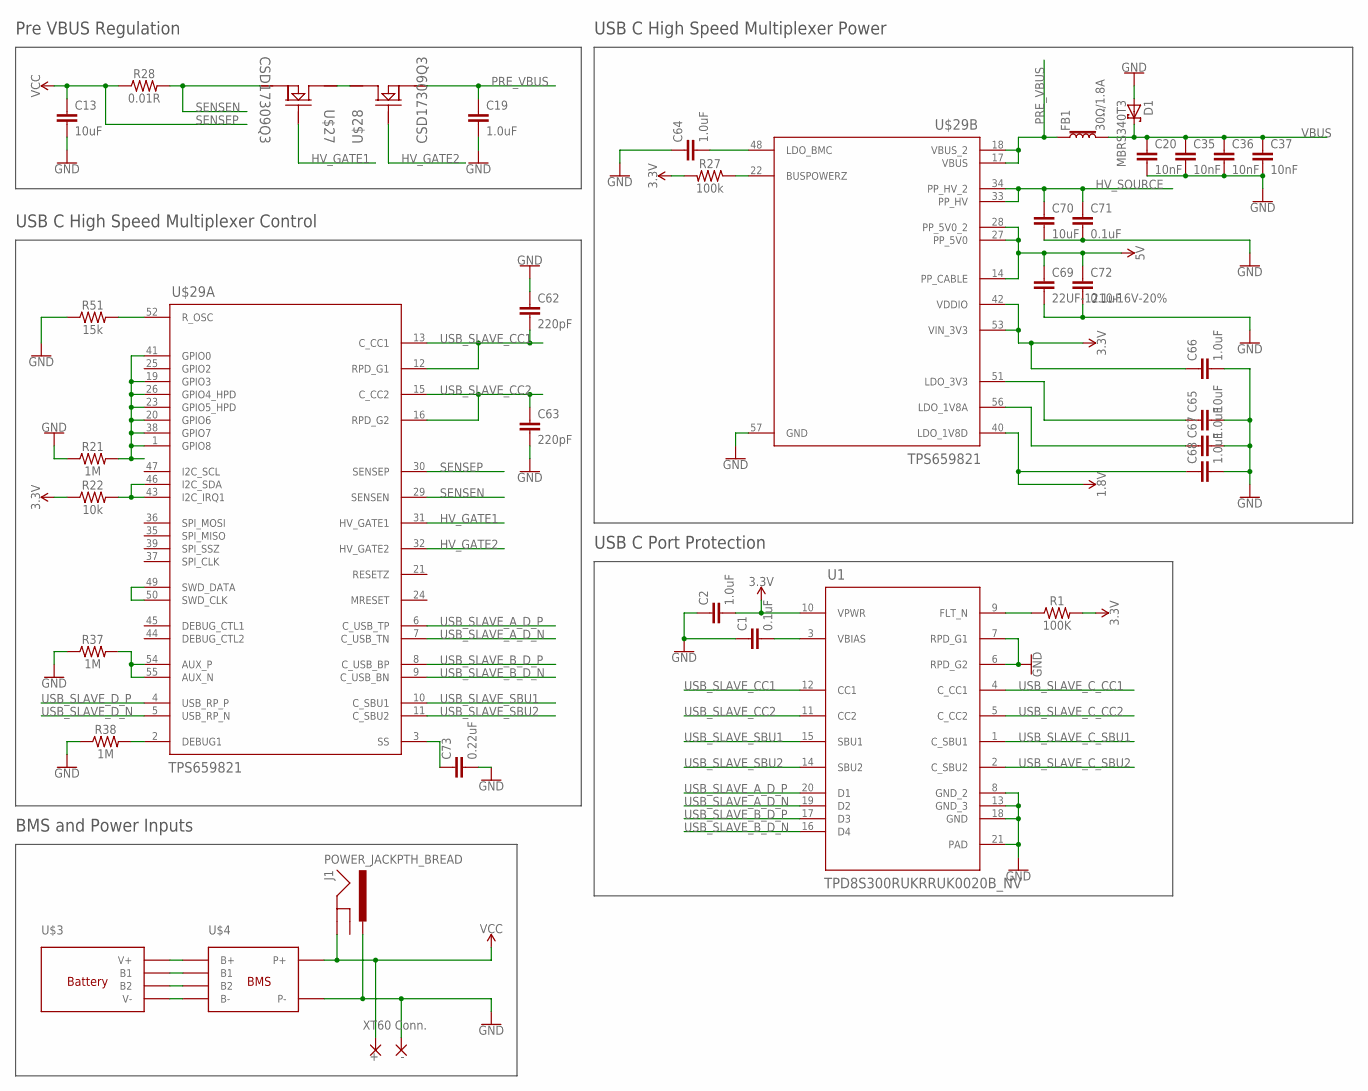
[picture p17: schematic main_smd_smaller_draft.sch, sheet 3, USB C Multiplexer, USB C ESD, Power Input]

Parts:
+: 3,81/1,1
-: 3,81/1,1
C1, C71, C72: 0.1uF; 0603
C2: 1.0uF; 0603
C13, C65, C70: 10uF; 1210
C19, C64, C66, C67, C68: 1.0uF; 1206
C20, C35, C36, C37: 10nF; 0603
C62, C63: 220pF; C0402
C69: 22UF-1210-16V-20%; 1210
C73: 0.22uF; 0603
D1: MBRS340T3; SMC
FB1: 30Ω/1.8A; 0603
J1: POWER_JACKPTH_BREAD; POWER_JACK_PTH_BREAD
R1: 100K; 0402
R21, R37, R38: 1M; 0603
R22: 10k; 0603
R27: 100k; 0603
R28: 0.01R; 0805
R51: 15k; 0603
U1: TPD8S300RUKRRUK0020B_NV; RUK0020B_NV
U$27, U$28: CSD17309Q3; DQG0008A
U$29: TPS659821; QFN50P800X800X100-57N

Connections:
1.8V: C68.1, U$29.40 (LDO_1V8D); also elsewhere on the board
3.3V: C2.2, C66.1, R1.2, R22.1, R27.2, U1.10 (VPWR), U$29.42 (VDDIO), U$29.53 (VIN_3V3); also elsewhere on the board
5V: C69.1, C72.1, U$29.14 (PP_CABLE), U$29.27 (PP_5V0), U$29.28 (PP_5V0_2); also elsewhere on the board
GND: -.1, C1.1, C2.1, C13.2, C19.2, C20.2, C35.2, C36.2, C37.2, C62.1, C63.2, C64.1, C65.2, C66.2, C67.2, C68.2, C69.2, C70.2, C71.2, C72.2, C73.2, D1.A, J1.PWR, R21.1, R37.1, R38.1, R51.1, U1.6 (RPD_G2), U1.7 (RPD_G1), U1.8 (GND_2), U1.13 (GND_3), U1.18 (GND), U1.21 (PAD), U$29.57 (GND); also elsewhere on the board
HV_GATE1: U$27.4 (GATE), U$29.31 (HV_GATE1)
HV_GATE2: U$28.4 (GATE), U$29.32 (HV_GATE2)
HV_SOURCE: C70.1, C71.1, U$29.33 (PP_HV), U$29.34 (PP_HV_2); also elsewhere on the board
LDO_3V3: C65.1, U$29.51 (LDO_3V3)
unnamed: R37.2, U$29.54 (AUX_P), U$29.55 (AUX_N)
unnamed: R27.1, U$29.22 (BUSPOWERZ)
unnamed: C64.2, U$29.48 (LDO_BMC)
unnamed: R21.2, U$29.1 (GPIO8), U$29.19 (GPIO3), U$29.20 (GPIO6), U$29.23 (GPIO5_HPD), U$29.26 (GPIO4_HPD), U$29.38 (GPIO7), U$29.41 (GPIO0)
unnamed: U$27.5 (DRAIN_2), U$27.6 (DRAIN_2), U$27.7 (DRAIN_2), U$27.8 (DRAIN_2), U$28.5 (DRAIN_2), U$28.6 (DRAIN_2), U$28.7 (DRAIN_2), U$28.8 (DRAIN_2)
unnamed: U$29.49 (SWD_DATA), U$29.50 (SWD_CLK)
unnamed: R22.2, U$29.43 (I2C_IRQ1), U$29.46 (I2C_SDA)
unnamed: R38.2, U$29.2 (DEBUG1)
unnamed: C73.1, U$29.3 (SS)
unnamed: R51.2, U$29.52 (R_OSC)
unnamed: C67.1, U$29.56 (LDO_1V8A)
unnamed: R1.1, U1.9 (FLT_N)
unnamed: C1.2, U1.3 (VBIAS)
PRE_VBUS: C19.1, FB1.1, U$28.1 (SOURCE_2), U$28.2 (SOURCE_2), U$28.3 (SOURCE_2), U$29.17 (VBUS), U$29.18 (VBUS_2)
SENSEN: R28.2, U$27.1 (SOURCE_2), U$27.2 (SOURCE_2), U$27.3 (SOURCE_2), U$29.29 (SENSEN)
SENSEP: C13.1, R28.1, U$29.30 (SENSEP)
USB_SLAVE_A_D_N: U1.19 (D2), U$29.7 (C_USB_TN); also elsewhere on the board
USB_SLAVE_A_D_P: U1.20 (D1), U$29.6 (C_USB_TP); also elsewhere on the board
USB_SLAVE_B_D_N: U1.16 (D4), U$29.9 (C_USB_BN); also elsewhere on the board
USB_SLAVE_B_D_P: U1.17 (D3), U$29.8 (C_USB_BP); also elsewhere on the board
USB_SLAVE_CC1: C62.2, U1.12 (CC1), U$29.12 (RPD_G1), U$29.13 (C_CC1)
USB_SLAVE_CC2: C63.1, U1.11 (CC2), U$29.15 (C_CC2), U$29.16 (RPD_G2)
USB_SLAVE_C_CC1: U1.4 (C_CC1); also elsewhere on the board
USB_SLAVE_C_CC2: U1.5 (C_CC2); also elsewhere on the board
USB_SLAVE_C_SBU1: U1.1 (C_SBU1); also elsewhere on the board
USB_SLAVE_C_SBU2: U1.2 (C_SBU2); also elsewhere on the board
USB_SLAVE_D_N: U$29.5 (USB_RP_N); also elsewhere on the board
USB_SLAVE_D_P: U$29.4 (USB_RP_P); also elsewhere on the board
USB_SLAVE_SBU1: U1.15 (SBU1), U$29.10 (C_SBU1)
USB_SLAVE_SBU2: U1.14 (SBU2), U$29.11 (C_SBU2)
VBUS: C20.1, C35.1, C36.1, C37.1, D1.C, FB1.2
VCC: +.1, J1.GND; also elsewhere on the board

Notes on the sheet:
Pre VBUS Regulation
USB C High Speed Multiplexer Control
USB C High Speed Multiplexer Power
XT60 Conn.
BMS and Power Inputs
USB C Port Protection

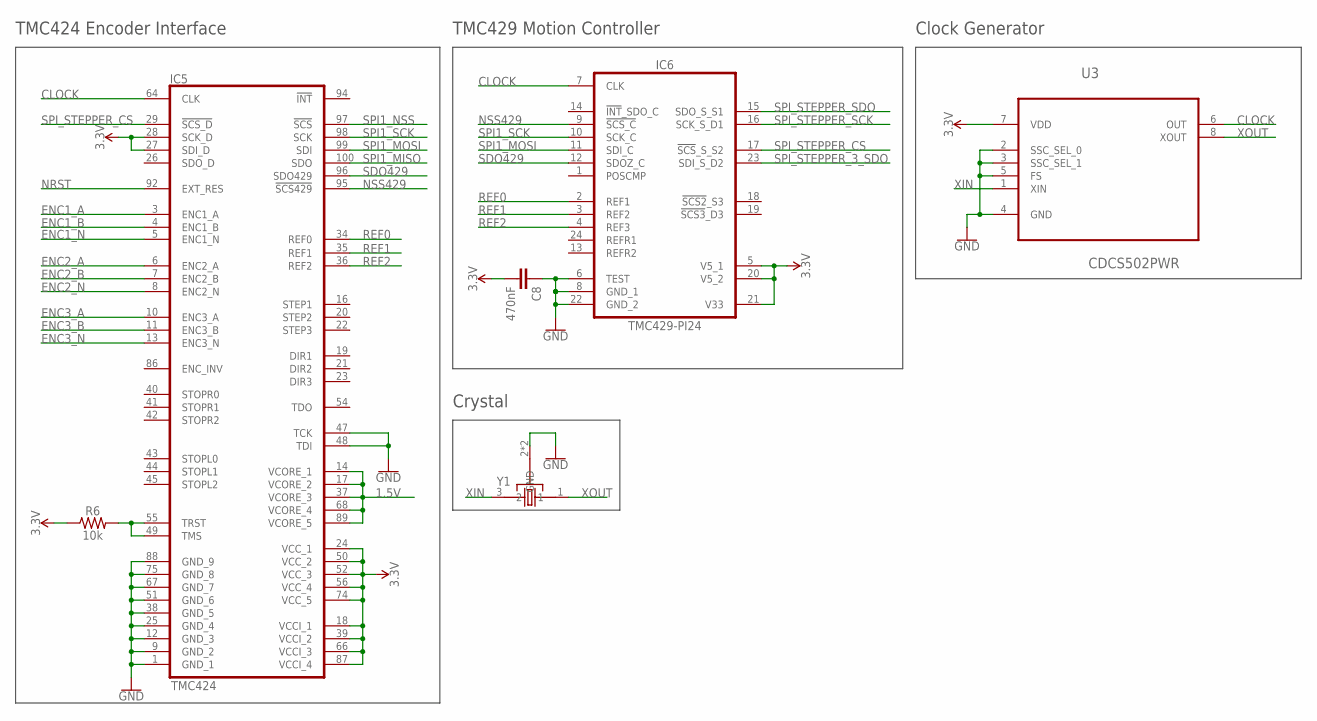
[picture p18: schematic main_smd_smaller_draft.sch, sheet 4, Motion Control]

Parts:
C8: 470nF; 0402
IC5: TMC424; TMC_TQFP100_0.5_14X14
IC6: TMC429-PI24; TMC_SO24_SOT137-1_1.27_15.5X7.5
R6: 10k; 0603
U3: CDCS502PWR; SOP65P640X120-8N
Y1: 7B-16.000MAAJ-T; 7B-16.000MAAJ-T_OSCSC500X320X105-4N

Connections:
1.5V: IC5.14 (VCORE_1), IC5.17 (VCORE_2), IC5.37 (VCORE_3), IC5.68 (VCORE_4), IC5.89 (VCORE_5); also elsewhere on the board
3.3V: C8.2, IC5.18 (VCCI_1), IC5.24 (VCC_1), IC5.27 (SDI_D), IC5.28 (SCK_D), IC5.39 (VCCI_2), IC5.50 (VCC_2), IC5.52 (VCC_3), IC5.56 (VCC_4), IC5.66 (VCCI_3), IC5.74 (VCC_5), IC5.87 (VCCI_4), IC6.5 (V5_1), IC6.20 (V5_2), IC6.21 (V33), R6.1, U3.7 (VDD); also elsewhere on the board
CLOCK: IC5.64 (CLK), IC6.7 (CLK), U3.6 (OUT); also elsewhere on the board
ENC1_A: IC5.3 (ENC1_A); also elsewhere on the board
ENC1_B: IC5.4 (ENC1_B); also elsewhere on the board
ENC1_N: IC5.5 (ENC1_N); also elsewhere on the board
ENC2_A: IC5.6 (ENC2_A); also elsewhere on the board
ENC2_B: IC5.7 (ENC2_B); also elsewhere on the board
ENC2_N: IC5.8 (ENC2_N); also elsewhere on the board
ENC3_A: IC5.10 (ENC3_A); also elsewhere on the board
ENC3_B: IC5.11 (ENC3_B); also elsewhere on the board
ENC3_N: IC5.13 (ENC3_N); also elsewhere on the board
GND: C8.1, IC5.1 (GND_1), IC5.9 (GND_2), IC5.12 (GND_3), IC5.25 (GND_4), IC5.38 (GND_5), IC5.47 (TCK), IC5.48 (TDI), IC5.51 (GND_6), IC5.67 (GND_7), IC5.75 (GND_8), IC5.88 (GND_9), IC6.6 (TEST), IC6.8 (GND_1), IC6.22 (GND_2), U3.2 (SSC_SEL_0), U3.3 (SSC_SEL_1), U3.4 (GND), U3.5 (FS), Y1.2 (GND), Y1.4 (GND); also elsewhere on the board
unnamed: IC5.49 (TMS), IC5.55 (TRST), R6.2
NRST: IC5.92 (EXT_RES); also elsewhere on the board
NSS429: IC5.95 (!SCS429), IC6.9 (!SCS_C)
REF0: IC5.34 (REF0), IC6.2 (REF1)
REF1: IC5.35 (REF1), IC6.3 (REF2)
REF2: IC5.36 (REF2), IC6.4 (REF3)
SDO429: IC5.96 (SDO429), IC6.12 (SDOZ_C)
SPI1_MISO: IC5.100 (SDO); also elsewhere on the board
SPI1_MOSI: IC5.99 (SDI), IC6.11 (SDI_C); also elsewhere on the board
SPI1_NSS: IC5.97 (!SCS); also elsewhere on the board
SPI1_SCK: IC5.98 (SCK), IC6.10 (SCK_C); also elsewhere on the board
SPI_STEPPER_3_SDO: IC6.23 (SDI_S_D2); also elsewhere on the board
SPI_STEPPER_CS: IC5.29 (!SCS_D), IC6.17 (!SCS!_S_S2); also elsewhere on the board
SPI_STEPPER_SCK: IC6.16 (SCK_S_D1); also elsewhere on the board
SPI_STEPPER_SDO: IC6.15 (SDO_S_S1); also elsewhere on the board
XIN: U3.1 (XIN), Y1.3 (2)
XOUT: U3.8 (XOUT), Y1.1

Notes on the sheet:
TMC424 Encoder Interface
TMC429 Motion Controller
Crystal
Clock Generator

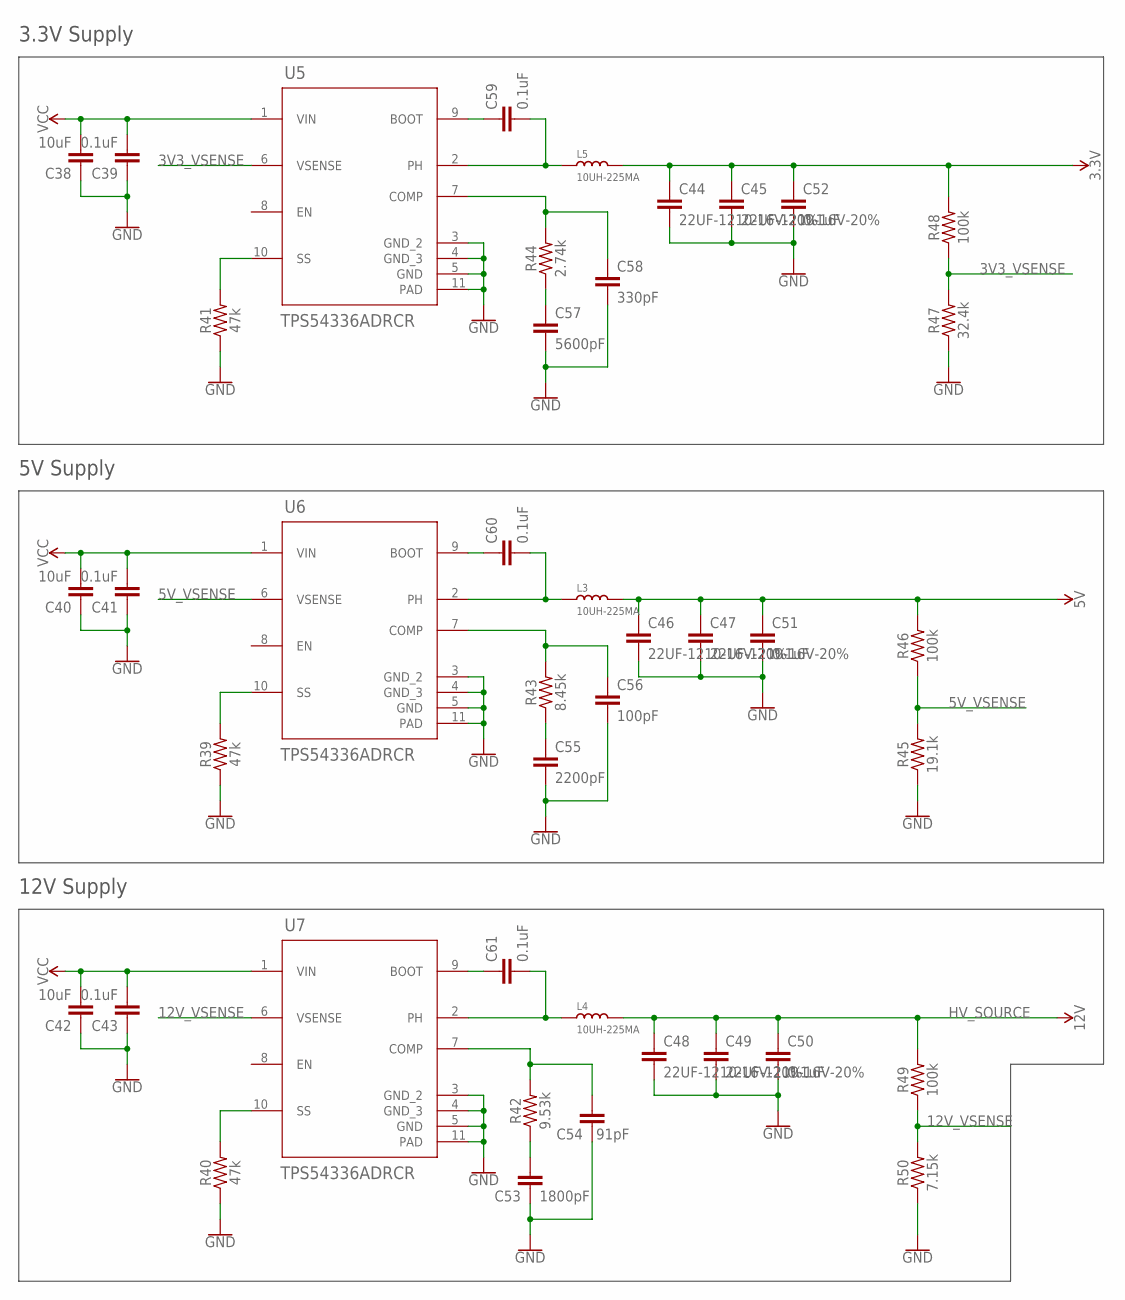
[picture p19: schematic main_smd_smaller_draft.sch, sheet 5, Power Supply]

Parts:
C38, C40, C42: 10uF; 1210
C39, C41, C43, C59, C60, C61: 0.1uF; 0603
C44, C45, C46, C47, C48, C49: 22UF-1210-16V-20%; 1210
C50, C51, C52: 0.1uF; 0402
C53: 1800pF; C0402
C54: 91pF; C0402
C55: 2200pF; C0402
C56: 100pF; C0402
C57: 5600pF; C0402
C58: 330pF; C0402
L3, L4, L5: 10UH-225MA; L0806
R39, R40, R41: 47k; 0603
R42: 9.53k; 0603
R43: 8.45k; 0603
R44: 2.74k; 0603
R45: 19.1k; 0603
R46, R48, R49: 100k; 0603
R47: 32.4k; 0603
R50: 7.15k; 0603
U5, U6, U7: TPS54336ADRCR; DRC0010J

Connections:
3.3V: C44.1, C45.1, C52.1, L5.2, R48.2; also elsewhere on the board
3V3_VSENSE: R47.2, R48.1, U5.6 (VSENSE)
5V: C46.1, C47.1, C51.1, L3.2, R46.2; also elsewhere on the board
5V_VSENSE: R45.2, R46.1, U6.6 (VSENSE)
12V_VSENSE: R49.1, R50.2, U7.6 (VSENSE)
GND: C38.1, C39.1, C40.1, C41.1, C42.1, C43.1, C44.2, C45.2, C46.2, C47.2, C48.2, C49.2, C50.2, C51.2, C52.2, C53.1, C54.1, C55.2, C56.2, C57.2, C58.2, R39.1, R40.1, R41.1, R45.1, R47.1, R50.1, U5.3 (GND_2), U5.4 (GND_3), U5.5 (GND), U5.11 (PAD), U6.3 (GND_2), U6.4 (GND_3), U6.5 (GND), U6.11 (PAD), U7.3 (GND_2), U7.4 (GND_3), U7.5 (GND), U7.11 (PAD); also elsewhere on the board
HV_SOURCE: C48.1, C49.1, C50.1, L4.2, R49.2; also elsewhere on the board
unnamed: R41.2, U5.10 (SS)
unnamed: R39.2, U6.10 (SS)
unnamed: R40.2, U7.10 (SS)
unnamed: C61.2, L4.1, U7.2 (PH)
unnamed: C60.2, L3.1, U6.2 (PH)
unnamed: C59.2, L5.1, U5.2 (PH)
unnamed: C61.1, U7.9 (BOOT)
unnamed: C59.1, U5.9 (BOOT)
unnamed: C60.1, U6.9 (BOOT)
unnamed: C53.2, R42.1
unnamed: C54.2, R42.2, U7.7 (COMP)
unnamed: C55.1, R43.1
unnamed: C56.1, R43.2, U6.7 (COMP)
unnamed: C57.1, R44.1
unnamed: C58.1, R44.2, U5.7 (COMP)
VCC: C38.2, C39.2, C40.2, C41.2, C42.2, C43.2, U5.1 (VIN), U6.1 (VIN), U7.1 (VIN); also elsewhere on the board

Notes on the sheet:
3.3V Supply
5V Supply
12V Supply

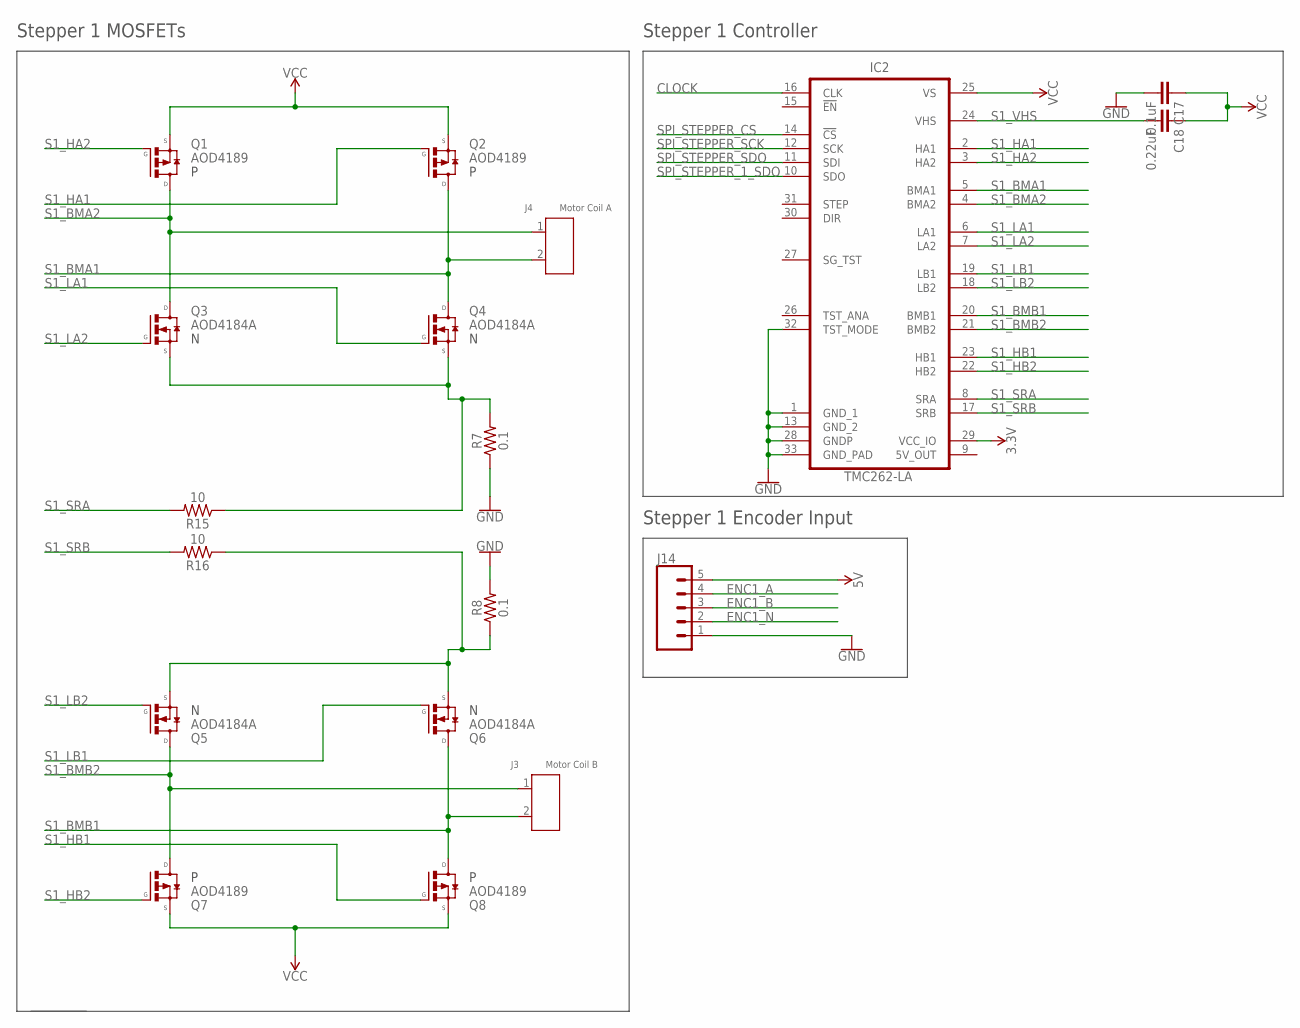
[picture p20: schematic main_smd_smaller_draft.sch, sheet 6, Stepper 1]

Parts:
C17: 0.1uF; 0402
C18: 0.22uF; 0603
IC2: TMC262-LA; TMC_QFN32_0.5_5.0X5.0
J3: Motor Coil B; H2-5.0-10.5X8.0MM
J4: Motor Coil A; H2-5.0-10.5X8.0MM
J14: CONN_05; 1X05
Q1, Q2, Q7, Q8: AOD4189; TO252
Q3, Q4, Q5, Q6: AOD4184A; TO252
R7, R8: 0.1; 1210
R15, R16: 10; 1206

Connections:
3.3V: IC2.29 (VCC_IO); also elsewhere on the board
5V: J14.5; also elsewhere on the board
CLOCK: IC2.16 (CLK); also elsewhere on the board
ENC1_A: J14.4; also elsewhere on the board
ENC1_B: J14.3; also elsewhere on the board
ENC1_N: J14.2; also elsewhere on the board
GND: C17.2, IC2.1 (GND_1), IC2.13 (GND_2), IC2.28 (GNDP), IC2.32 (TST_MODE), IC2.33 (GND_PAD), J14.1, R7.1, R8.2; also elsewhere on the board
unnamed: Q5.R (S), Q6.R (S), R8.1, R16.1
unnamed: Q3.R (S), Q4.R (S), R7.2, R15.1
S1_BMA1: IC2.5 (BMA1), J4.2, Q2.C (D), Q4.C (D)
S1_BMA2: IC2.4 (BMA2), J4.1, Q1.C (D), Q3.C (D)
S1_BMB1: IC2.20 (BMB1), J3.2, Q6.C (D), Q8.C (D)
S1_BMB2: IC2.21 (BMB2), J3.1, Q5.C (D), Q7.C (D)
S1_HA1: IC2.2 (HA1), Q2.L (G)
S1_HA2: IC2.3 (HA2), Q1.L (G)
S1_HB1: IC2.23 (HB1), Q8.L (G)
S1_HB2: IC2.22 (HB2), Q7.L (G)
S1_LA1: IC2.6 (LA1), Q4.L (G)
S1_LA2: IC2.7 (LA2), Q3.L (G)
S1_LB1: IC2.19 (LB1), Q6.L (G)
S1_LB2: IC2.18 (LB2), Q5.L (G)
S1_SRA: IC2.8 (SRA), R15.2
S1_SRB: IC2.17 (SRB), R16.2
S1_VHS: C18.2, IC2.24 (VHS)
SPI_STEPPER_1_SDO: IC2.10 (SDO); also elsewhere on the board
SPI_STEPPER_CS: IC2.14 (!CS!); also elsewhere on the board
SPI_STEPPER_SCK: IC2.12 (SCK); also elsewhere on the board
SPI_STEPPER_SDO: IC2.11 (SDI); also elsewhere on the board
VCC: C17.1, C18.1, IC2.25 (VS), Q1.R (S), Q2.R (S), Q7.R (S), Q8.R (S); also elsewhere on the board

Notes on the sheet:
Stepper 1 MOSFETs
Stepper 1 Controller
Stepper 1 Encoder Input

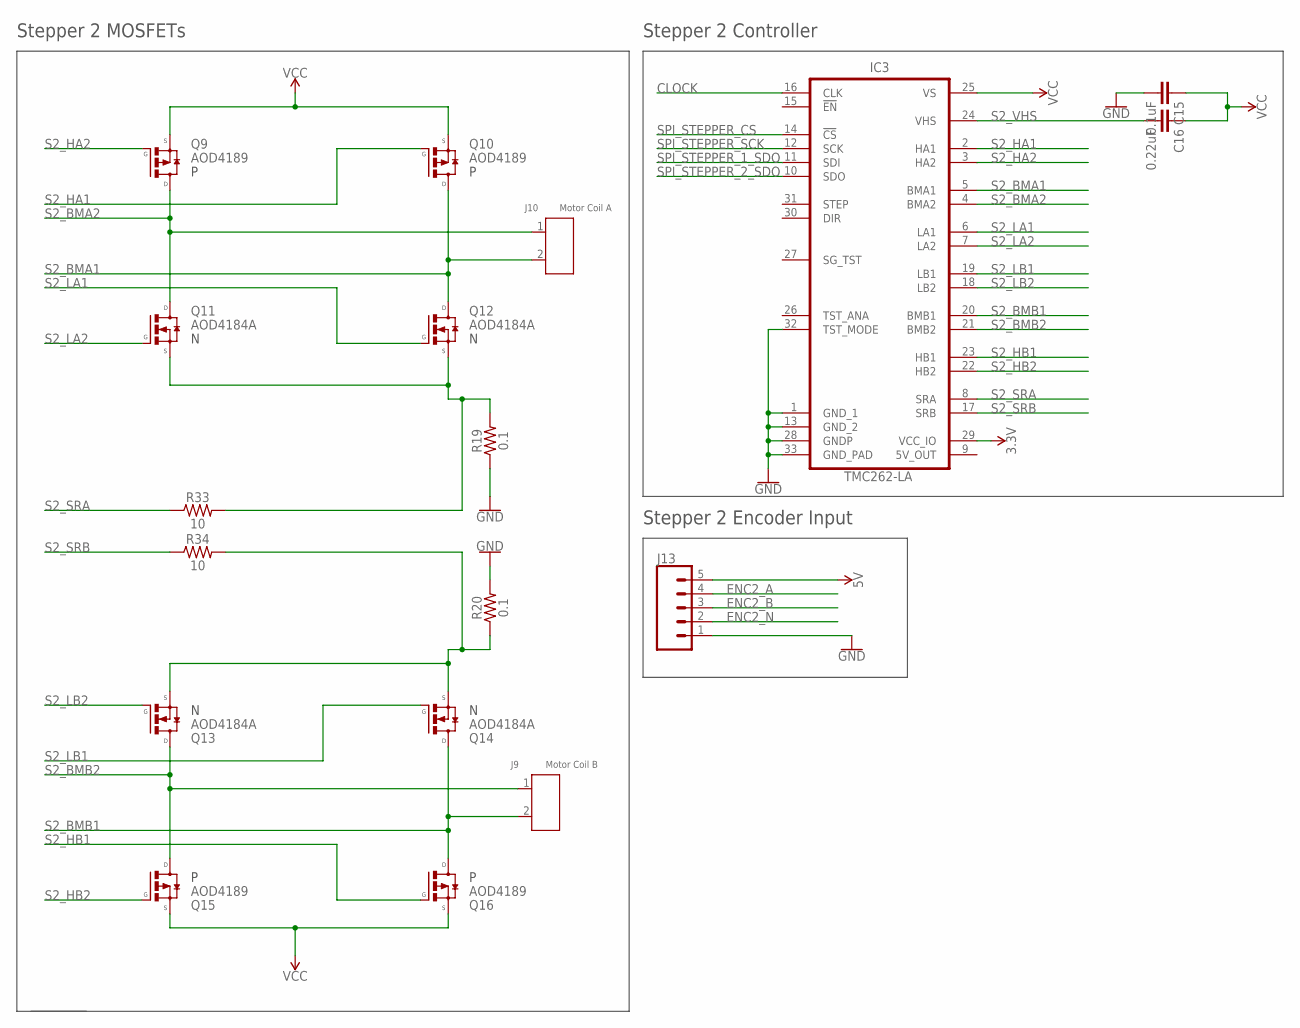
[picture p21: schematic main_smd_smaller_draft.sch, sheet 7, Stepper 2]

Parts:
C15: 0.1uF; 0402
C16: 0.22uF; 0603
IC3: TMC262-LA; TMC_QFN32_0.5_5.0X5.0
J9: Motor Coil B; H2-5.0-10.5X8.0MM
J10: Motor Coil A; H2-5.0-10.5X8.0MM
J13: CONN_05; 1X05
Q9, Q10, Q15, Q16: AOD4189; TO252
Q11, Q12, Q13, Q14: AOD4184A; TO252
R19, R20: 0.1; 1210
R33, R34: 10; 1206

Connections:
3.3V: IC3.29 (VCC_IO); also elsewhere on the board
5V: J13.5; also elsewhere on the board
CLOCK: IC3.16 (CLK); also elsewhere on the board
ENC2_A: J13.4; also elsewhere on the board
ENC2_B: J13.3; also elsewhere on the board
ENC2_N: J13.2; also elsewhere on the board
GND: C15.2, IC3.1 (GND_1), IC3.13 (GND_2), IC3.28 (GNDP), IC3.32 (TST_MODE), IC3.33 (GND_PAD), J13.1, R19.1, R20.2; also elsewhere on the board
unnamed: Q11.R (S), Q12.R (S), R19.2, R33.2
unnamed: Q13.R (S), Q14.R (S), R20.1, R34.2
S2_BMA1: IC3.5 (BMA1), J10.2, Q10.C (D), Q12.C (D)
S2_BMA2: IC3.4 (BMA2), J10.1, Q9.C (D), Q11.C (D)
S2_BMB1: IC3.20 (BMB1), J9.2, Q14.C (D), Q16.C (D)
S2_BMB2: IC3.21 (BMB2), J9.1, Q13.C (D), Q15.C (D)
S2_HA1: IC3.2 (HA1), Q10.L (G)
S2_HA2: IC3.3 (HA2), Q9.L (G)
S2_HB1: IC3.23 (HB1), Q16.L (G)
S2_HB2: IC3.22 (HB2), Q15.L (G)
S2_LA1: IC3.6 (LA1), Q12.L (G)
S2_LA2: IC3.7 (LA2), Q11.L (G)
S2_LB1: IC3.19 (LB1), Q14.L (G)
S2_LB2: IC3.18 (LB2), Q13.L (G)
S2_SRA: IC3.8 (SRA), R33.1
S2_SRB: IC3.17 (SRB), R34.1
S2_VHS: C16.2, IC3.24 (VHS)
SPI_STEPPER_1_SDO: IC3.11 (SDI); also elsewhere on the board
SPI_STEPPER_2_SDO: IC3.10 (SDO); also elsewhere on the board
SPI_STEPPER_CS: IC3.14 (!CS!); also elsewhere on the board
SPI_STEPPER_SCK: IC3.12 (SCK); also elsewhere on the board
VCC: C15.1, C16.1, IC3.25 (VS), Q9.R (S), Q10.R (S), Q15.R (S), Q16.R (S); also elsewhere on the board

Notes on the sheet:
Stepper 2 MOSFETs
Stepper 2 Controller
Stepper 2 Encoder Input

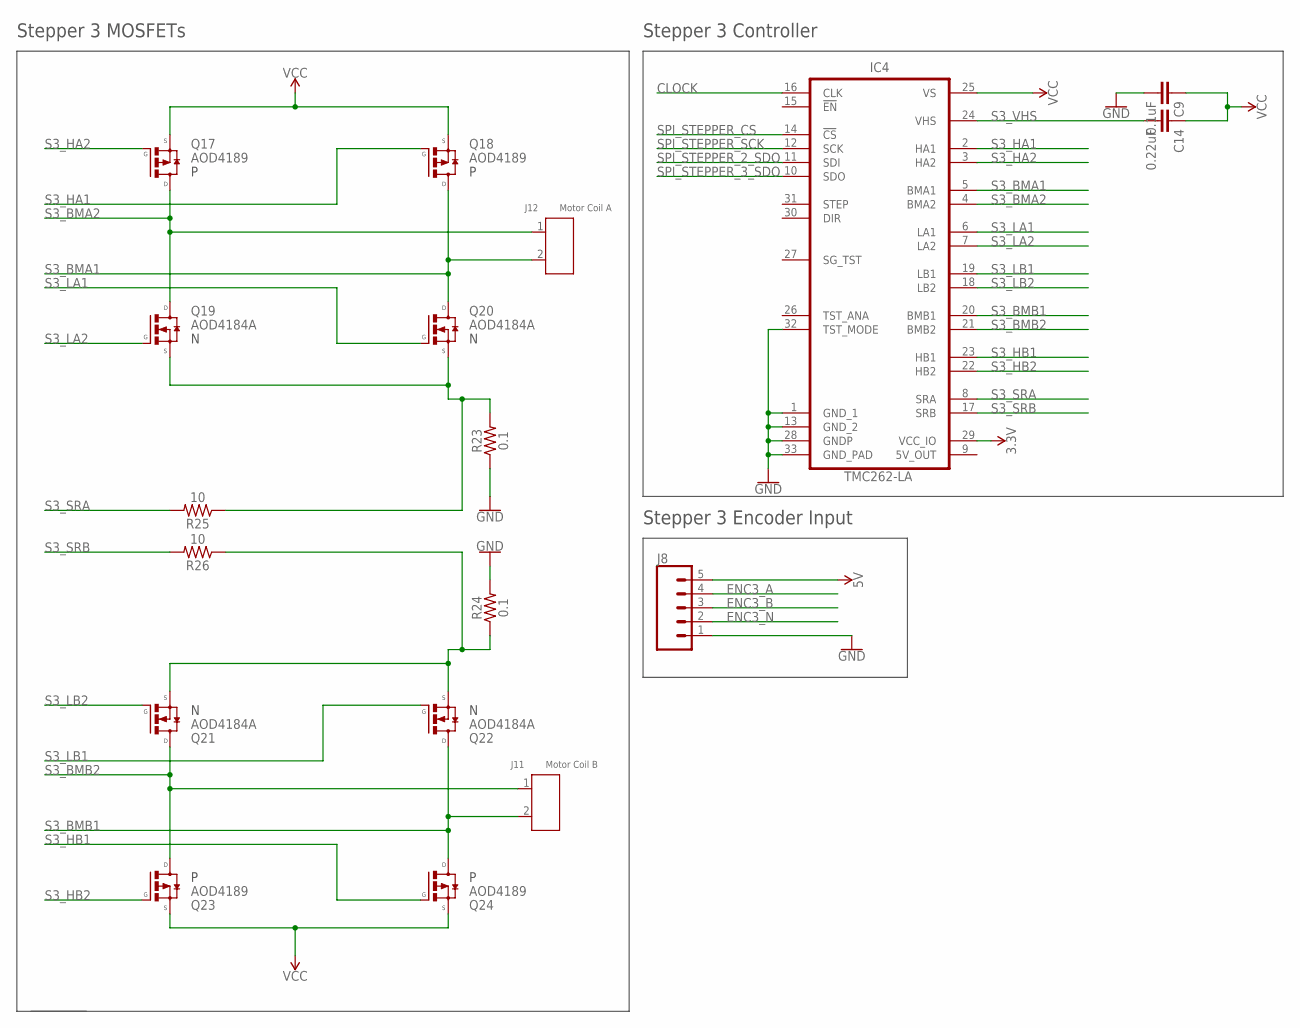
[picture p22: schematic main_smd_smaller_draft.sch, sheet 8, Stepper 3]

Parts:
C9: 0.1uF; 0402
C14: 0.22uF; 0603
IC4: TMC262-LA; TMC_QFN32_0.5_5.0X5.0
J8: CONN_05; 1X05
J11: Motor Coil B; H2-5.0-10.5X8.0MM
J12: Motor Coil A; H2-5.0-10.5X8.0MM
Q17, Q18, Q23, Q24: AOD4189; TO252
Q19, Q20, Q21, Q22: AOD4184A; TO252
R23, R24: 0.1; 1210
R25, R26: 10; 1206

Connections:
3.3V: IC4.29 (VCC_IO); also elsewhere on the board
5V: J8.5; also elsewhere on the board
CLOCK: IC4.16 (CLK); also elsewhere on the board
ENC3_A: J8.4; also elsewhere on the board
ENC3_B: J8.3; also elsewhere on the board
ENC3_N: J8.2; also elsewhere on the board
GND: C9.2, IC4.1 (GND_1), IC4.13 (GND_2), IC4.28 (GNDP), IC4.32 (TST_MODE), IC4.33 (GND_PAD), J8.1, R23.1, R24.2; also elsewhere on the board
unnamed: Q19.R (S), Q20.R (S), R23.2, R25.1
unnamed: Q21.R (S), Q22.R (S), R24.1, R26.1
S3_BMA1: IC4.5 (BMA1), J12.2, Q18.C (D), Q20.C (D)
S3_BMA2: IC4.4 (BMA2), J12.1, Q17.C (D), Q19.C (D)
S3_BMB1: IC4.20 (BMB1), J11.2, Q22.C (D), Q24.C (D)
S3_BMB2: IC4.21 (BMB2), J11.1, Q21.C (D), Q23.C (D)
S3_HA1: IC4.2 (HA1), Q18.L (G)
S3_HA2: IC4.3 (HA2), Q17.L (G)
S3_HB1: IC4.23 (HB1), Q24.L (G)
S3_HB2: IC4.22 (HB2), Q23.L (G)
S3_LA1: IC4.6 (LA1), Q20.L (G)
S3_LA2: IC4.7 (LA2), Q19.L (G)
S3_LB1: IC4.19 (LB1), Q22.L (G)
S3_LB2: IC4.18 (LB2), Q21.L (G)
S3_SRA: IC4.8 (SRA), R25.2
S3_SRB: IC4.17 (SRB), R26.2
S3_VHS: C14.2, IC4.24 (VHS)
SPI_STEPPER_2_SDO: IC4.11 (SDI); also elsewhere on the board
SPI_STEPPER_3_SDO: IC4.10 (SDO); also elsewhere on the board
SPI_STEPPER_CS: IC4.14 (!CS!); also elsewhere on the board
SPI_STEPPER_SCK: IC4.12 (SCK); also elsewhere on the board
VCC: C9.1, C14.1, IC4.25 (VS), Q17.R (S), Q18.R (S), Q23.R (S), Q24.R (S); also elsewhere on the board

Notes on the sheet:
Stepper 3 MOSFETs
Stepper 3 Controller
Stepper 3 Encoder Input

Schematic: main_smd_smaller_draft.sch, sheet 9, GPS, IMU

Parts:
C3, C75: 10nF; 0603
C4, C5, C7: 0.1uF; 0402
C6: 10uF; 0603
C74: 1.0uF; 0402
IC1: S1315F8_RAW; S1315F8_SMT
J5: 73100-0114
U4: LSM9DS1; PQFN24P43_350X300X102L35X23N

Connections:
3.3V: C5.1, C6.1, C7.1, C74.1, C75.1, IC1.5 (VBAT), IC1.11 (VCC33), U4.1 (VDDIO), U4.3 (VDDIO), U4.22 (VDD), U4.23 (VDD); also elsewhere on the board
ANTENNA_GND: IC1.2 (AGND), IC1.3 (AGND), IC1.4 (AGND), IC1.26 (AGND), IC1.28 (AGND), IC1.29 (AGND), IC1.33 (AGND), IC1.35 (AGND), IC1.36 (AGND), J5.2 (GND), J5.3 (GND), J5.4 (GND), J5.5 (GND)
ANTENNA_IN: IC1.1 (RFIN), J5.1 (RF)
GND: C3.2, C4.2, C5.2, C6.2, C7.2, C74.2, C75.2, IC1.6 (GND), IC1.9 (GND), IC1.10 (GND), IC1.12 (GND), IC1.15 (GND), IC1.17 (GND), IC1.19 (GND), IC1.21 (GND), IC1.22 (GND), IC1.23 (GND), IC1.24 (GND), U4.14 (RES), U4.15 (RES), U4.16 (RES), U4.17 (RES), U4.18 (RES), U4.19 (GND), U4.20 (GND); also elsewhere on the board
unnamed: C4.1, U4.24 (C1)
unnamed: C3.1, U4.21 (CAP)
SPI3_MISO: U4.5 (SDO_A/G), U4.6 (SDO_M); also elsewhere on the board
SPI3_MOSI: U4.4 (SDA/SDI/SDO); also elsewhere on the board
SPI3_NSS1: U4.8 (CS_M); also elsewhere on the board
SPI3_NSS2: U4.7 (CS_A/G); also elsewhere on the board
SPI3_SCK: U4.2 (SCL/SPC); also elsewhere on the board
USART1_RX: IC1.30 (TXD0); also elsewhere on the board
USART1_TX: IC1.31 (RXD0); also elsewhere on the board

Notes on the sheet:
GPS
IMU

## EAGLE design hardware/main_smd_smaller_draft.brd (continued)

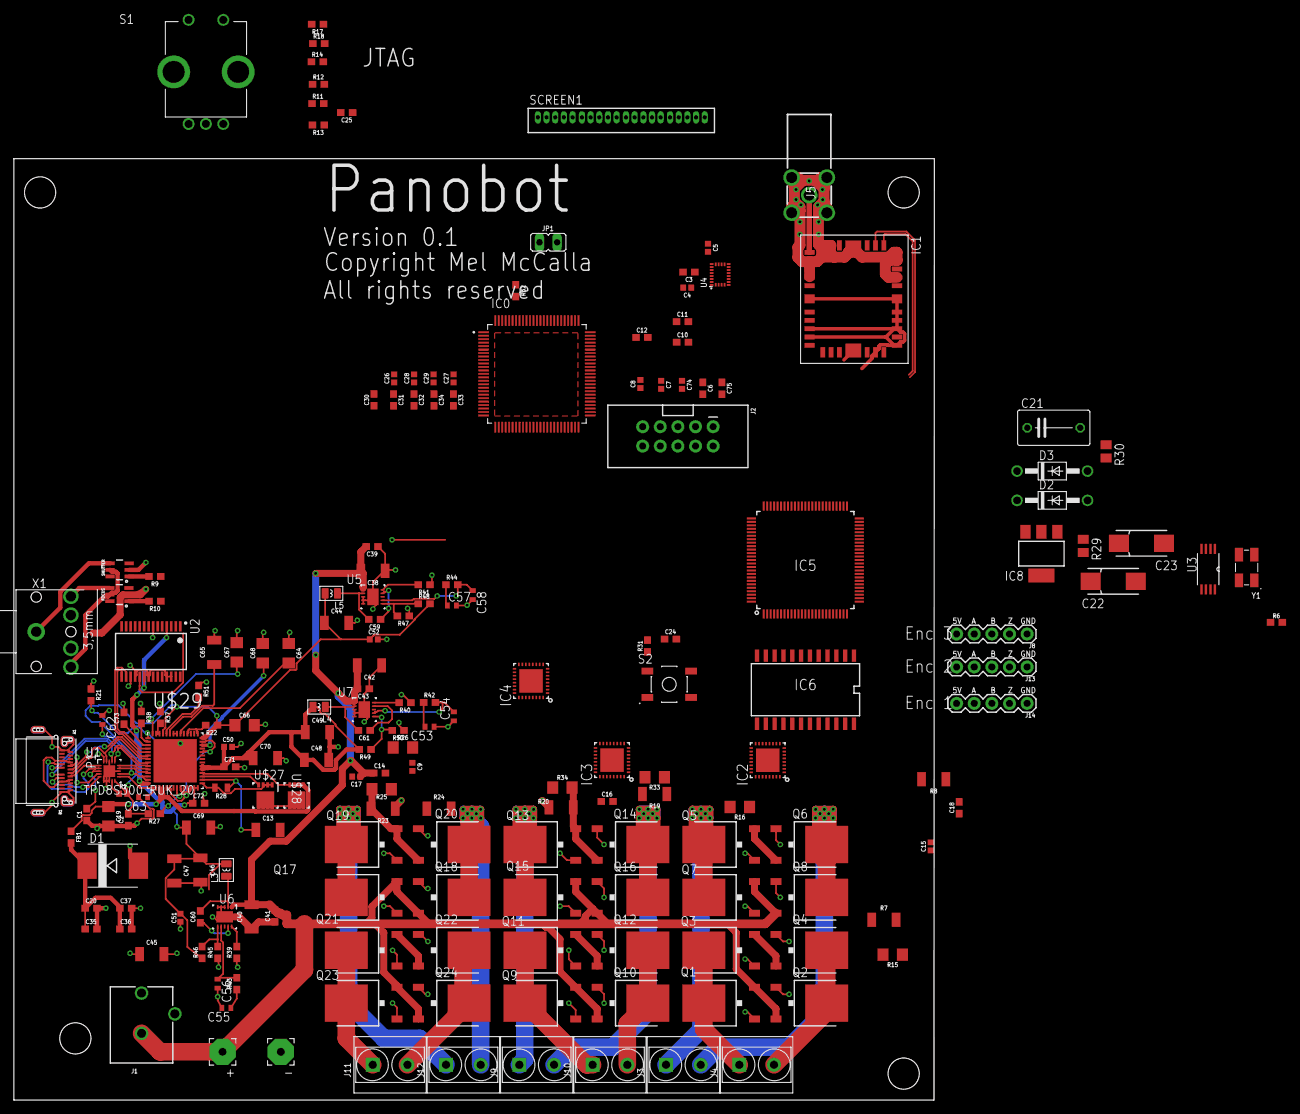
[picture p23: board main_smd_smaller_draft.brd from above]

Board: 4 copper layers, 132.7 x 135.7 mm, 192 parts (0 on the bottom side), 180 nets.

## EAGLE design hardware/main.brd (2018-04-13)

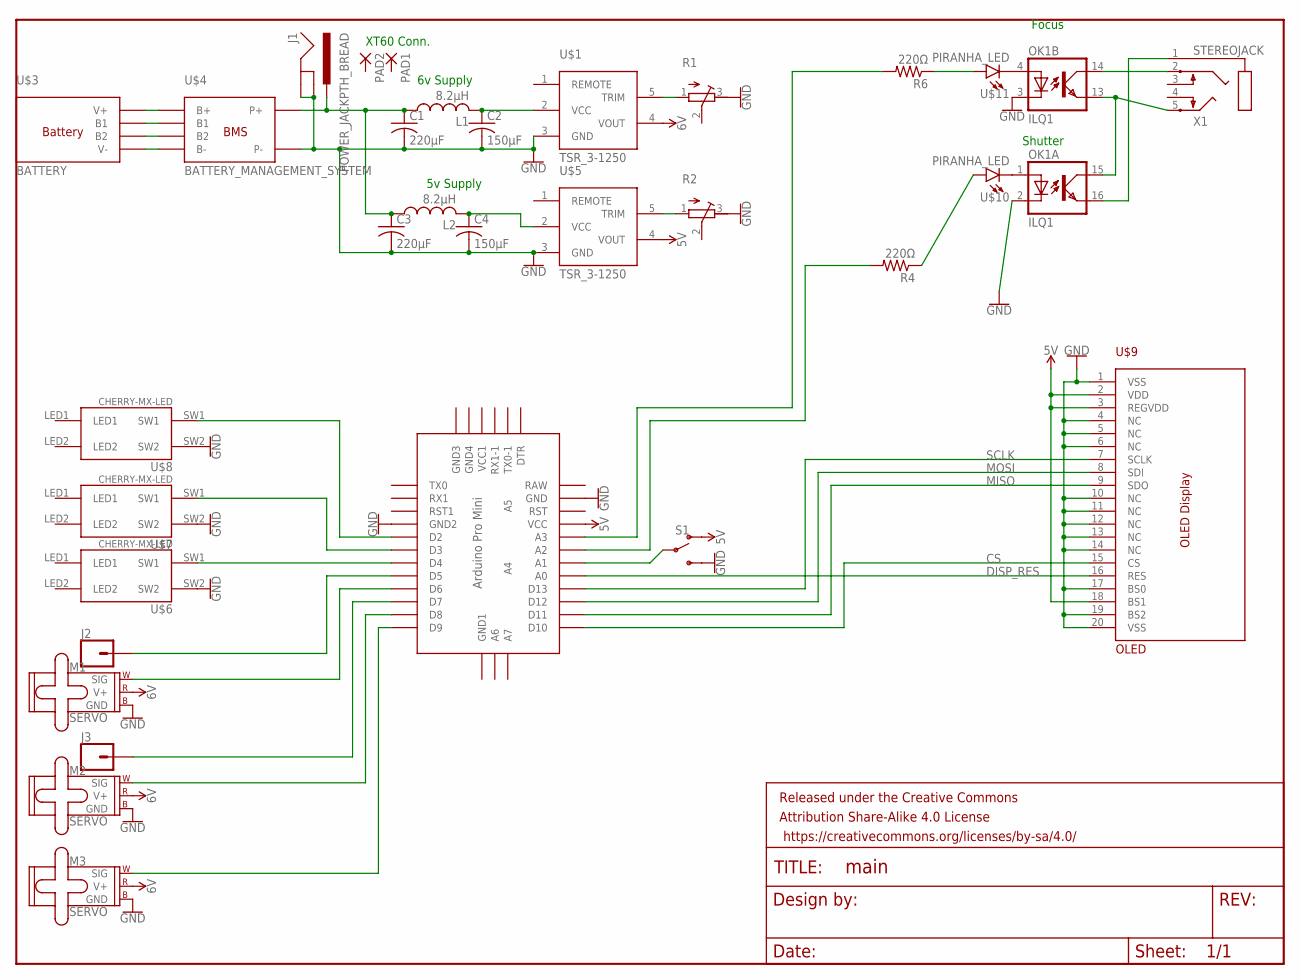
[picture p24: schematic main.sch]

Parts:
C1, C3: 220µF; C075-032X103
C2, C4: 150µF; C075-032X103
FRAME1: FRAME-LETTER; CREATIVE_COMMONS
J1: POWER_JACKPTH_BREAD; POWER_JACK_PTH_BREAD
J2, J3: CONN_01; 1X01
L1, L2: 8.2µH; IRF-1
M1, M2, M3: SERVO; 1X03
OK1: ILQ1; DIL16
PAD1, PAD2: 3,81/1,1
R1, R2: R-TRIMM64W; RTRIM64W
R4, R6: 220Ω; 0207/10
S1: SWITCH-SPDT-PTH-11.6X4.0MM; SWITCH_SPDT_PTH_11.6X4.0MM
U$1, U$5: TSR_3-1250; SIP-5
U$2: ABK-PRO-MINI
U$6, U$7, U$8: CHERRY-MX-LED
U$9: OLED; SIP-20
U$10, U$11: PIRANHA_LED; LED_PIRANHA_5MM
X1: STEREOJACK; STX3100

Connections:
5V: S1.1 (O), U$2.VCC, U$5.4 (VOUT), U$9.2 (VDD), U$9.3 (REGVDD), U$9.18 (BS1)
6V: M1.2 (V+), M2.2 (V+), M3.2 (V+), U$1.4 (VOUT)
BUTTON_1: U$2.D2, U$8.SW1
BUTTON_2: U$2.D3, U$7.SW1
BUTTON_3: U$2.D4, U$6.SW1
CS: U$2.D10, U$9.15 (CS)
DISP_RES: U$2.A0, U$9.16 (RES)
FOCUS: R6.2, U$2.A3
GND: C1.2, C2.2, C3.2, C4.2, J1.GND, J1.GNDBREAK, M1.3 (GND), M2.3 (GND), M3.3 (GND), OK1.2 (C), OK1.3 (C), R1.3 (E), R2.3 (E), S1.3 (S), U$1.3 (GND), U$2.GND, U$2.GND1 (GND2), U$5.3 (GND), U$6.SW2, U$7.SW2, U$8.SW2, U$9.1 (VSS), U$9.4 (NC), U$9.5 (NC), U$9.6 (NC), U$9.10 (NC), U$9.11 (NC), U$9.12 (NC), U$9.13 (NC), U$9.14 (NC), U$9.17 (BS0), U$9.19 (BS2), U$9.20 (VSS)
MISO: U$2.D11, U$9.9 (SDO)
MODE_SWITCH: S1.2, U$2.A1
MOSI: U$2.D12, U$9.8 (SDI)
unnamed: OK1.14 (COL), X1.2
unnamed: OK1.16 (EMIT), X1.1
unnamed: OK1.4 (A), U$11.+@0 (C), U$11.+@1 (C)
unnamed: C2.1, L1.2, U$1.2 (VCC)
unnamed: R1.1 (A), U$1.5 (TRIM)
unnamed: C4.1, L2.2, U$5.2 (VCC)
unnamed: R2.1 (A), U$5.5 (TRIM)
unnamed: R6.1, U$11.-@0 (A), U$11.-@1 (A)
unnamed: R4.1, U$10.-@0 (A), U$10.-@1 (A)
unnamed: OK1.1 (A), U$10.+@0 (C), U$10.+@1 (C)
unnamed: OK1.13 (EMIT), OK1.15 (COL), X1.5
P+: C1.1, C3.1, J1.PWR, L1.1, L2.1
SCLK: U$2.D13, U$9.7 (SCLK)
SERVO_1_CONTROL: M1.1 (SIG), U$2.D6
SERVO_1_FEEDBACK: J2.1, U$2.D5
SERVO_2_CONTROL: M2.1 (SIG), U$2.D8
SERVO_2_FEEDBACK: J3.1, U$2.D7
SERVO_3_CONTROL: M3.1 (SIG), U$2.D9
SHUTTER: R4.2, U$2.A2

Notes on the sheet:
XT60 Conn.
5v Supply
6v Supply
Shutter
Focus

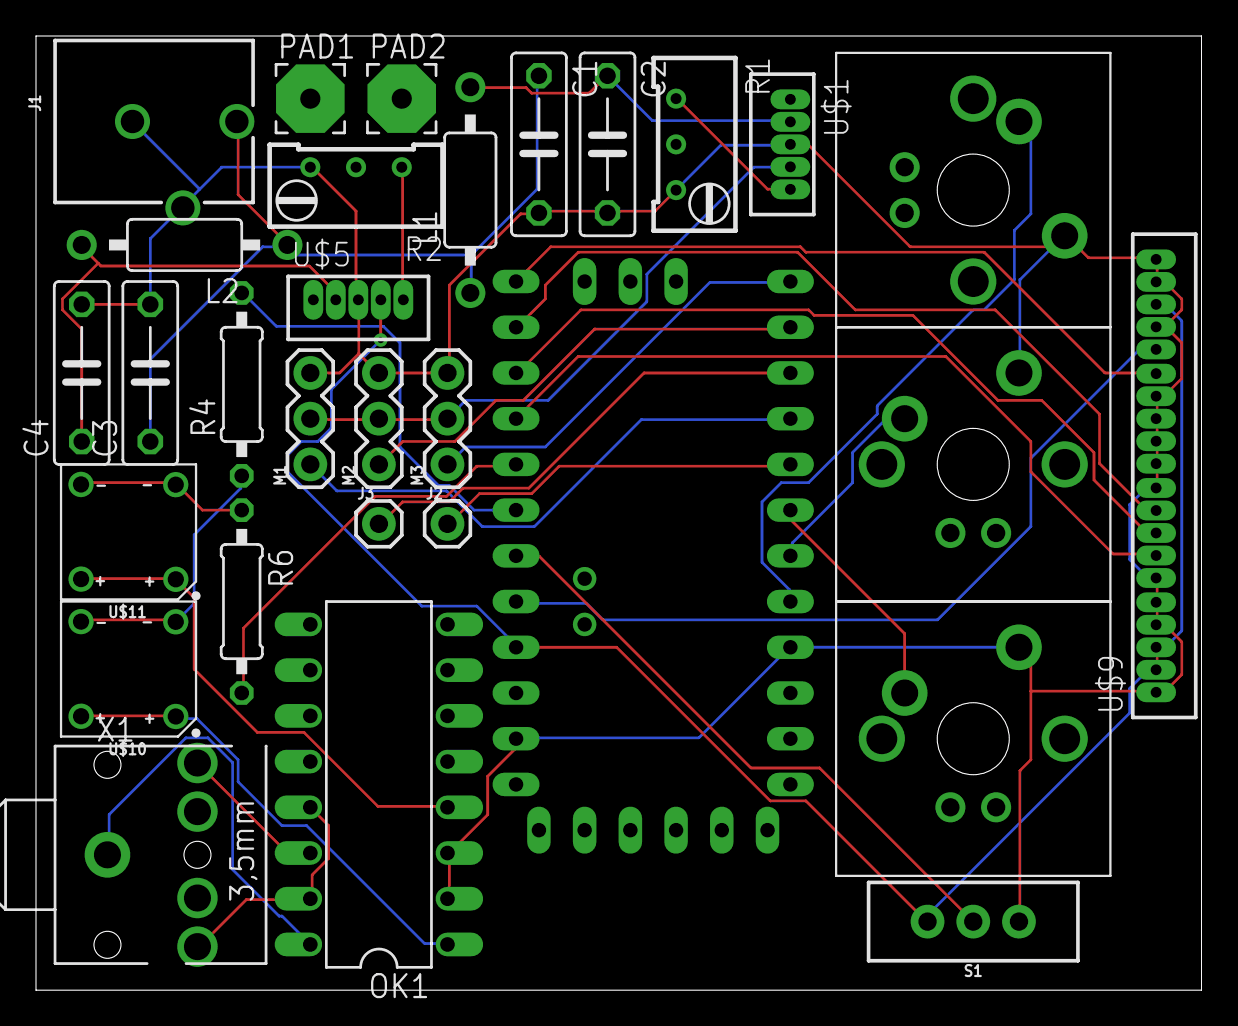
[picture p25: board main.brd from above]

Board: 2 copper layers, 64.8 x 53.0 mm, 31 parts (0 on the bottom side), 31 nets.

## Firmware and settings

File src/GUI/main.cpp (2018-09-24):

/*******************************************************************************
 * main.cpp
 * Copyright (C) 2018 Mel McCalla <melmccalla@gmail.com>
 *
 * This file is part of panoBot.
 *
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
 * You should have received a copy of the GNU General Public License
 * along with panoBot.  If not, see <http://www.gnu.org/licenses/>.
 *******************************************************************************/

#include "MainWindow.hpp"

#include <gtkmm/application.h>
#include <glibmm/i18n.h>

int main(int argc, char* argv[]) {
	setlocale (LC_ALL, "");
	bindtextdomain(GETTEXT_PACKAGE, PROGRAMNAME_LOCALEDIR);
	bind_textdomain_codeset(GETTEXT_PACKAGE, "UTF-8");
	textdomain(GETTEXT_PACKAGE);

	auto app = Gtk::Application::create(argc, argv, "com.github.panoBot-GUI");

	MainWindow window;

	return app->run(window);
}

/*gtk::application stored in smartpointer,
 checks args passed, standard options such ass
 --display*/

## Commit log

2018-02-13 Added cmake and eagle files
    [main.brd, main.sch]
2018-02-21 Updated CMakeLists.txt to fix baud rate for arduino
2018-02-22 Updated arduino core to the latest version
2018-02-22 Updated hardware files for eagle
    [main.brd, main.sch]
2018-02-22 No longer using Arduino Core library
    For some reason, binaries linked with the Arduino Core library refuse to
    run. For this reason, this project will be using raw AVR C.
    [main.cpp]
2018-02-22 Updated cmake/avr-arduino-toolchain.cmake
2018-03-11 updated servo code
2018-03-11 updated button code, and pid loop to recieve servo control
2018-03-13 Added Camera folder
2018-03-13 Added Buttons folder
2018-03-13 Updated hardware
    [main.brd, main.sch]
2018-03-13 Updated camera code to use new delay functions
2018-03-13 Updated PID loop
2018-03-14 testing servo running
2018-03-14 Updated servo code for testing
2018-03-14 test another servo
2018-03-14 Updated servotest and display
2018-03-14 Added missing semicolon and formatted Display.cpp
    [Display.cpp]
2018-03-14 Servos now work. Updated servo code.
2018-04-13 Cleaned up schematic and board layout
    [main.brd, main.sch]
2018-04-18 Added missing function declaration in Servo.hpp
    [Servo.cpp]
2018-05-30 Finished SMD board layout for hardware
    [main_smd.brd, main_smd.csv, main_smd.sch]
2018-09-24 Updated hardware directory and other misc updates
    [main_smd.brd, main_smd.csv, main_smd.dxf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]

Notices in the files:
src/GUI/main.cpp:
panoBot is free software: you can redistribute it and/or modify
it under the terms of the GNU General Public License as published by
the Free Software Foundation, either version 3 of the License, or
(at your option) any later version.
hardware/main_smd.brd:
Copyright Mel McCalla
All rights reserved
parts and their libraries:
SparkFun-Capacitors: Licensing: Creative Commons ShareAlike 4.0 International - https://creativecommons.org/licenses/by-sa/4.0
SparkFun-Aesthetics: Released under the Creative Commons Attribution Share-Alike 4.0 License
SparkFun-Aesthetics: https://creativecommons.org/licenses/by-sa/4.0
